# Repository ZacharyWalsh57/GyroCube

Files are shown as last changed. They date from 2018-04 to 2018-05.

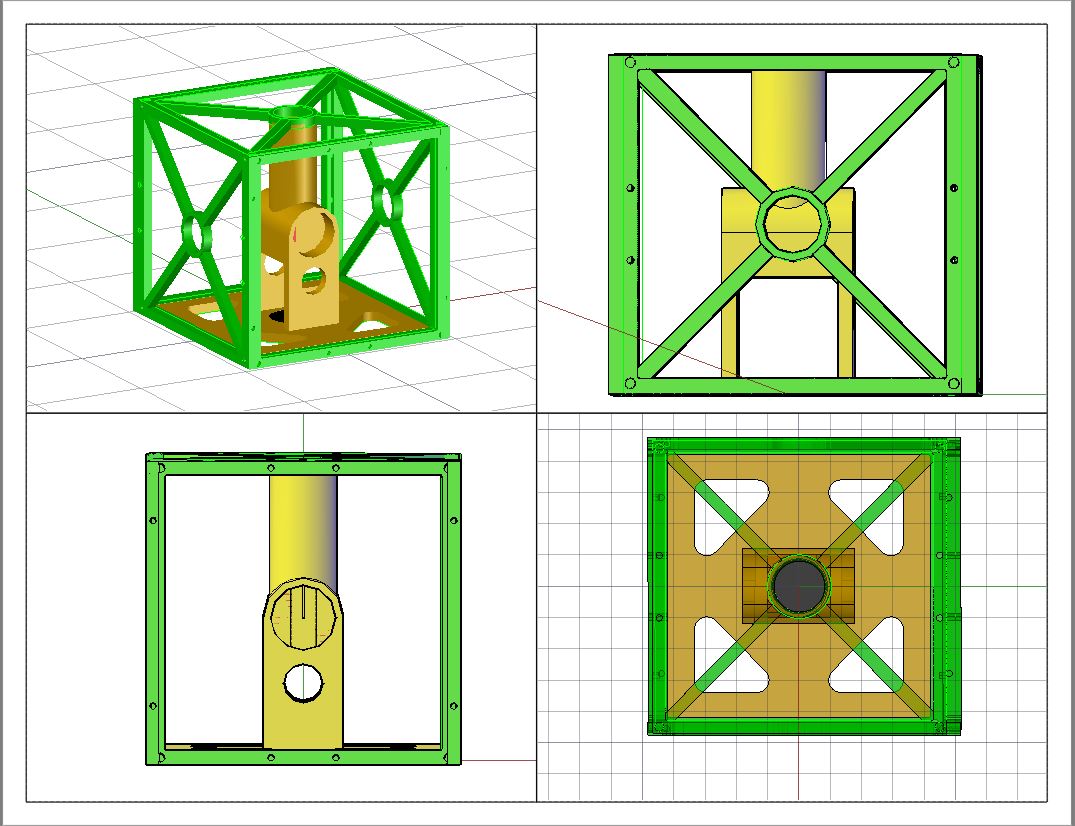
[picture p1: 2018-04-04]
3D Printing and CAD/Layout Model Views/Cube Frame V2 - Built Solid.JPG

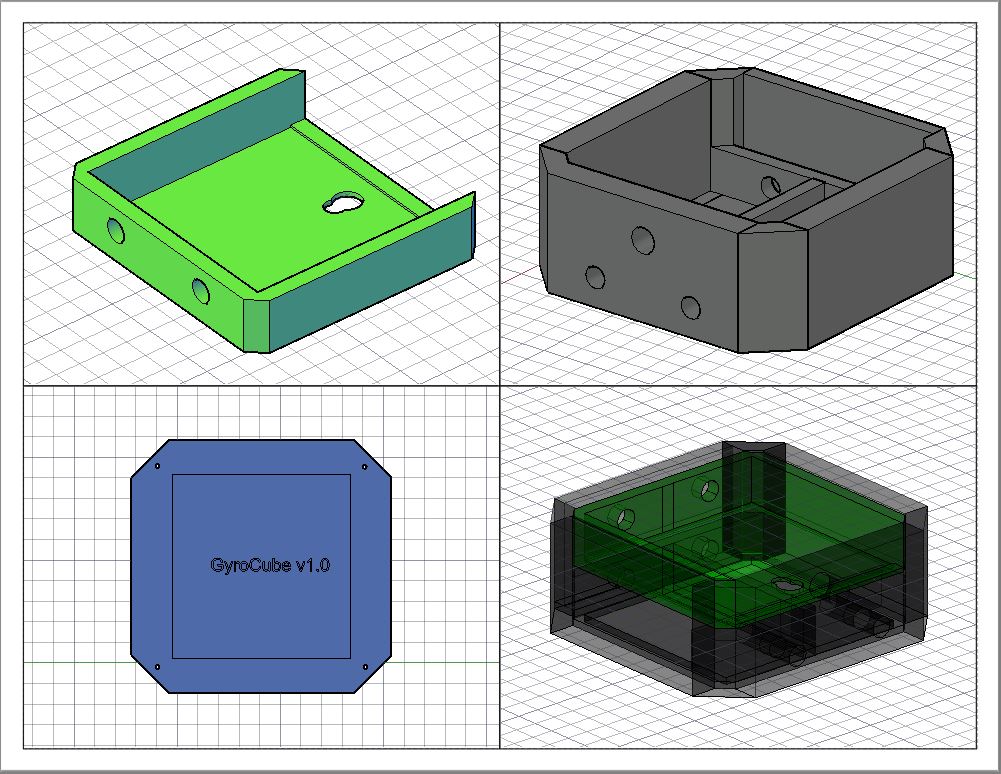
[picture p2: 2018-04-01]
3D Printing and CAD/Layout Model Views/Control Box Split View.JPG

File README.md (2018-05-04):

# GyroCube

The PID (Or maybe even PD) based, arduino powered, self balancing cube!

----------------------------------------------------------------------------------------------------------------------------------------
5/3/18:
After finally getting a new IMU and some other parts, development is back on track.  First round of progress updates is on 5/8/18.
Hopefully by then we'll have:
- A working setup loop which proves all the parts work.
- A 99% functional PID loop
- No more memory issues (Please. Running with 79% SRAM usage is painful)
- And finally, a prety good part of our presentation done. If all goes well, this might somehow work

Whats new?
- New IMU: Waveshare 10DOF IMU with an MPU9255 sensor on it (so more new libraries)
- Fully functional LCD
- Soon to be rewritten code to store more things in EEPROM and use writeMillis instead of analog write for motor speeds.

----------------------------------------------------------------------------------------------------------------------------------------

4/7/18:
It somehow didn't take that long to do a full rebuild.  The second version is up and running with stronger parts and better wiring.

Some things added now:
- PLA Soldered the parts together.  Looks bad but works wonders.
- Fixed motor vibrations
- Added in new sketch that lets us find the zero point of the MPU since we cant seem to fix the calibrations any other way.
- Also threw up diagrams for the control box and the three voltage dividers we will use for battery life monitoring.  

------------------------------------------------------------------------------------------------------------------------------------------

4/6/18:
- Well unfortunately thing took a turn for the worst.  We're left with no choice but to rebuild the whole cube from the ground up.  The repo will remain the same but will probably branch into version 1.5 leaving the main one behind. Code will be the same for basic component setup, but maybe some pins will change.  

What went wrong you might ask? Basically anything we could have imagined.
- Motor flywheels were unbalanced and caused incredible amounts of vibration.
- Hardware used to hold the cube together ripped the sides apart and caused instability.
- The MPU6050 wiring wasn't done 100% perfectly and the leads ripped out of the breakout board.
- When doing a 90% throttle test with the flywheels on, one of the flywheels heated up and expanded off of the motor completly ripping apart the entire cube.  That's the biggest problem we had.  

In the next version, as mentioned before code will remain the same for the most part, but we will likley either move to the Processing IDE or hook the system up to MATLAB (ugh) for GUI based data and tuning.

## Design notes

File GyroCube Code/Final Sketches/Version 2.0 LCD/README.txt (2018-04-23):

V2 Setup for the Cube. Going to be doing some stuff differently since
I just found out that were out of local variable space.  Anything that 
changes, thats going into the normal flash.  Anything else is staying
away. 

Wire - LEDs and I2C Mapping
Servo - Used for the ESCs.  
I2CDev - Used for addressing the MPU
MPU6050... - Used to setup the MPU.
LiquidCrystal - LCD wiring
LiquidMenu - LCD Menus (Gonna take a lot of space....)
Button - Simple button library.  Keeps code neat.
EEPROM - Storing something eventually...

------------------------------------------------------------------------
Variables:
Define all the NEVER CHANGING PINS:
LEDs pins dont move
MOTORS dont move
MOTOR pulse rates are constant.
MPU Pins dont move (Don't need to worry)
LCD Pins dont move
Button Pins do not move
MPU Variables

Then use all the menu text and write it in one shot. 
Might consider moving it into progspace if things get tight.
Really would rather not. EDIT: I did lol

Create LCD Screens and menus and the System
Create the button pins and the button objects
Create the Servos
Create the MPU
Create the LED pins
------------------------------------------------------------------------
SETUP:
Start LCD
Start Servos and attach pins
pinMode LEDs
At least init the MPU maybe?
Open Serial monitor
-print out raw debug level things
Setup Telem output (later on)
Set the LCD focus points for each display.
------------------------------------------------------------------------

HELPER FUNCTIONS:

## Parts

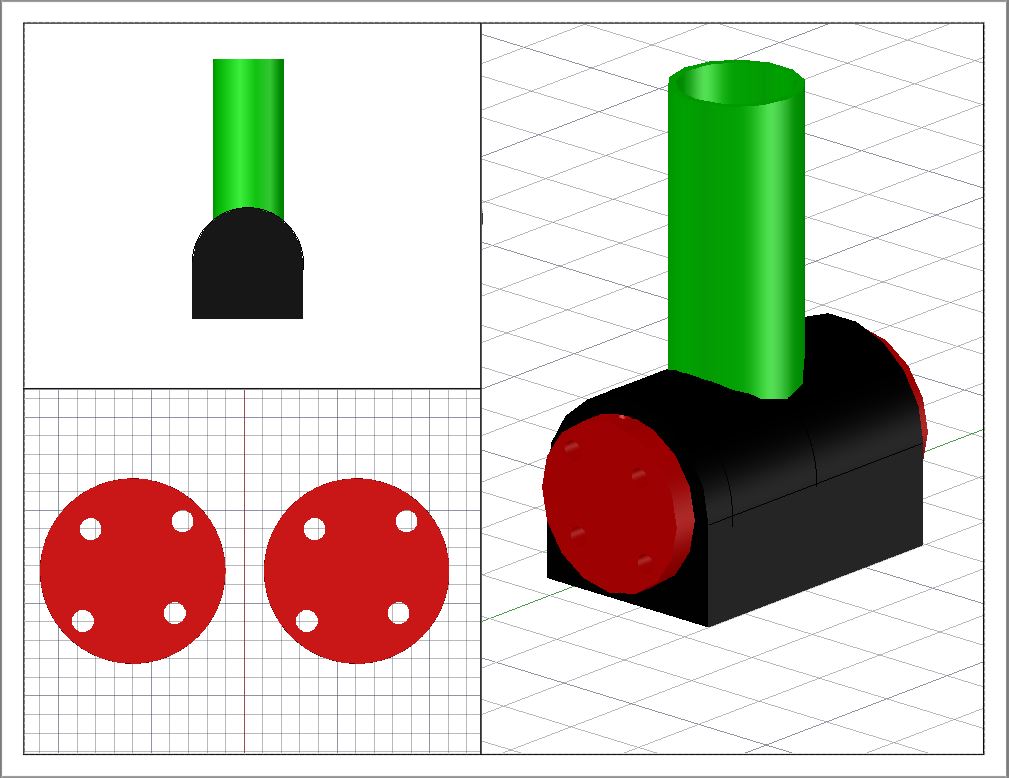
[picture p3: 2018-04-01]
3D Printing and CAD/Layout Model Views/Motor Mounting Parts.JPG

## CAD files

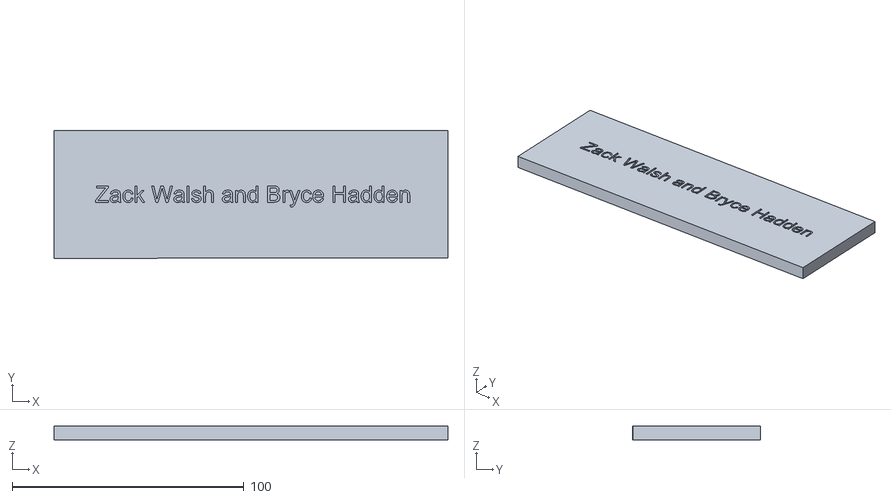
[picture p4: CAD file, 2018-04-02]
3D Printing and CAD/Battery Box Schematics/STLs/Battery Box - Top Cover - V1.stl
170.0 x 55.0 x 6.00

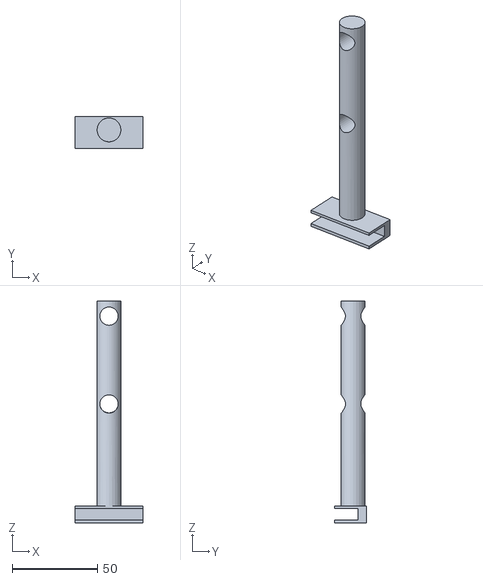
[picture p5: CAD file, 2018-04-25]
3D Printing and CAD/Control Box Schematics/STLs/Wire Clip - V3.0.stl
40.0 x 18.5 x 130.0

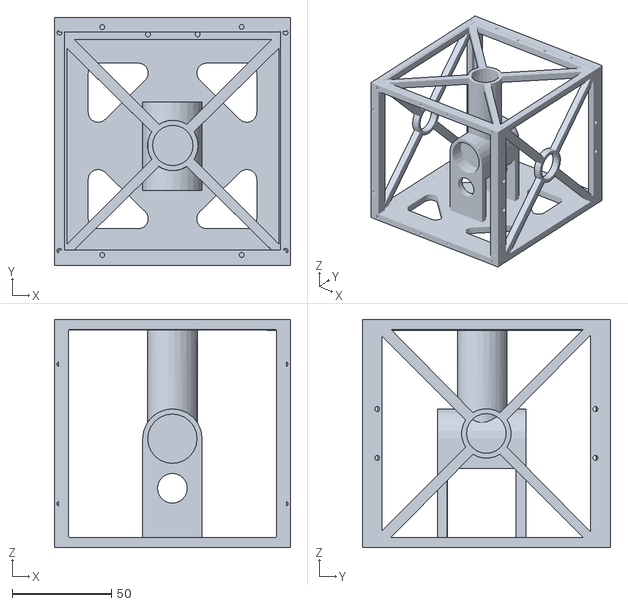
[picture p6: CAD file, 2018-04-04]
3D Printing and CAD/Cube Schematics/Version 1 - Split Parts/STLs/GyroCube Built Frame - SOLID FRAME - V2.stl
119.0 x 125.1 x 115.0

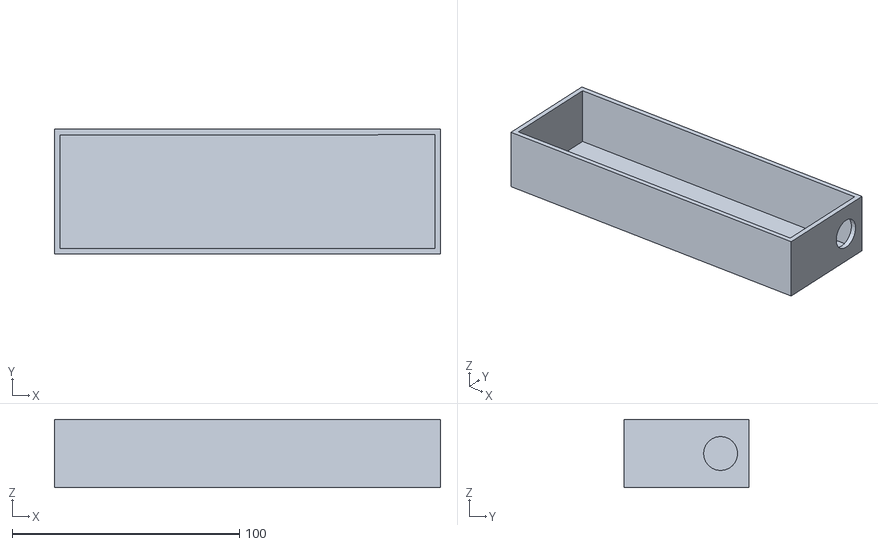
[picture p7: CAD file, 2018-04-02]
3D Printing and CAD/Battery Box Schematics/STLs/Battery Box - Bottom - V1.stl
170.0 x 55.0 x 30.0

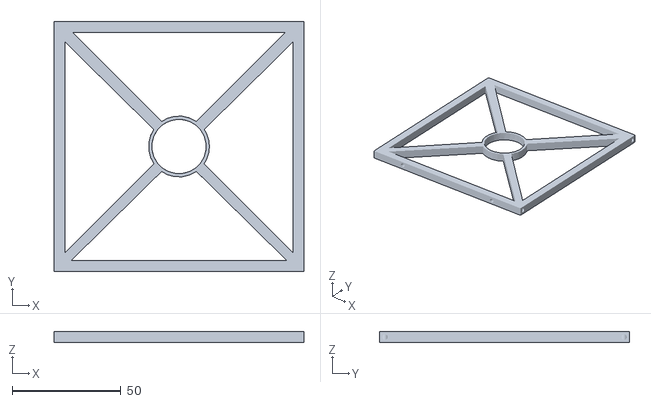
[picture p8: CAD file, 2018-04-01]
3D Printing and CAD/Cube Schematics/Version 1 - Split Parts/STLs/GyroCube TOP SIDE - STL.stl
115.0 x 115.0 x 5.14

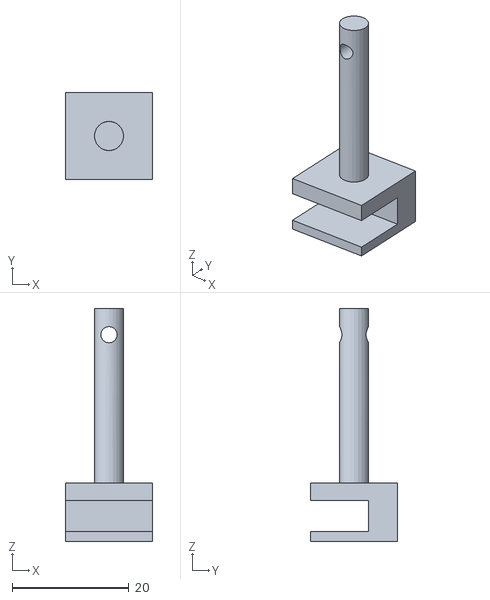
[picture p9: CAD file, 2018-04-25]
3D Printing and CAD/Control Box Schematics/STLs/Wire Clip - V1.,0.stl
15.0 x 15.0 x 40.0

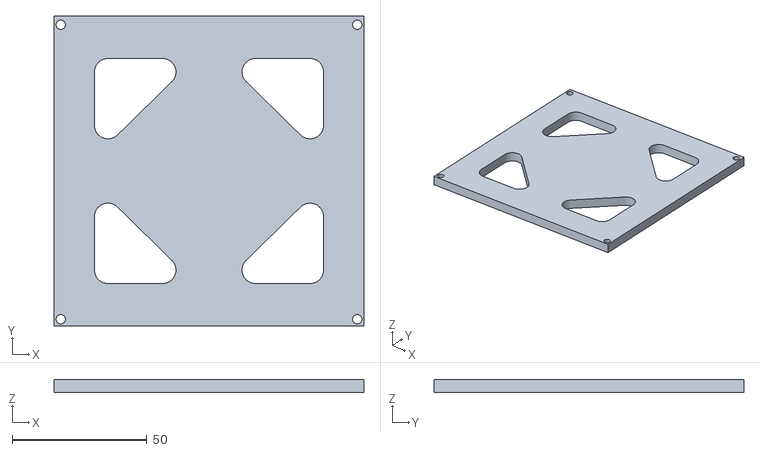
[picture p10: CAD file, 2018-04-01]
3D Printing and CAD/Cube Schematics/Version 1 - Split Parts/STLs/GyroCube Bottom Side - STL.stl
115.0 x 115.0 x 5.00

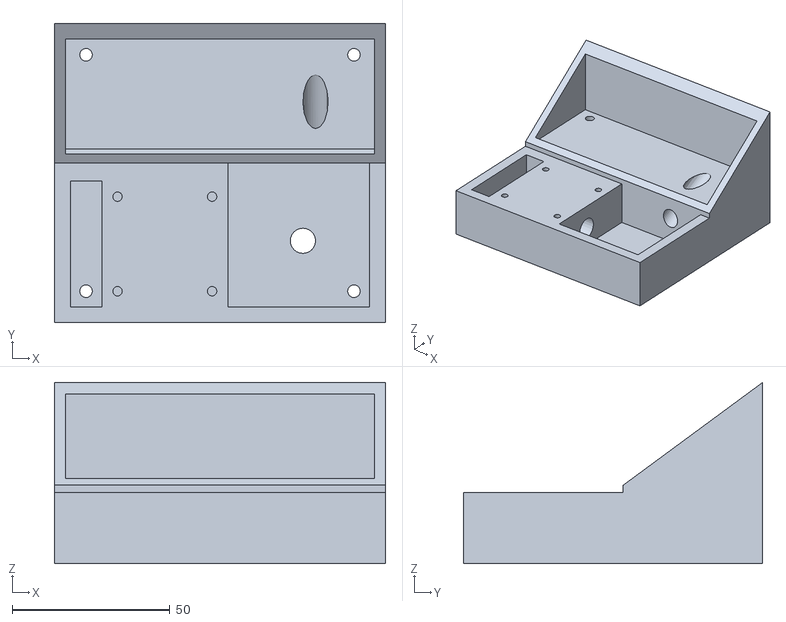
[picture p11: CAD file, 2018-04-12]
3D Printing and CAD/Control Box Schematics/STLs/LCD and KEYPAD Control Box TOP_1.stl
105.0 x 95.0 x 57.5

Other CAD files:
3D Printing and CAD/Battery Box Schematics/DWGs/Battery Box with Top.dwg
3D Printing and CAD/Control Box Schematics/CAD Drawings/Wire Clip - V1.,0.dwg
3D Printing and CAD/Cube Schematics/Version 1 - Split Parts/CAD Models/HDD Flywheel Model.dwg
3D Printing and CAD/Cube Schematics/Version 2 - Solid Prints/CAD Models/GyroCube Built Frame V2 - SOLID BOTTOM.dwg
3D Printing and CAD/Control Box Schematics/CAD Drawings/LCD and KEYPAD Control Box TOP.dwg
3D Printing and CAD/Cube Schematics/Version 1 - Split Parts/CAD Models/GyroCube Bottom Side - CAD.dwg
3D Printing and CAD/Cube Schematics/Version 2 - Solid Prints/CAD Models/GyroCube Built Frame - V2.dwg
3D Printing and CAD/Control Box Schematics/CAD Drawings/LCD and KEYPAD Control Box TOP_recover.dwg
3D Printing and CAD/Cube Schematics/Version 1 - Split Parts/CAD Models/GyroCube Open Sides EXTENDED - CAD.dwg
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

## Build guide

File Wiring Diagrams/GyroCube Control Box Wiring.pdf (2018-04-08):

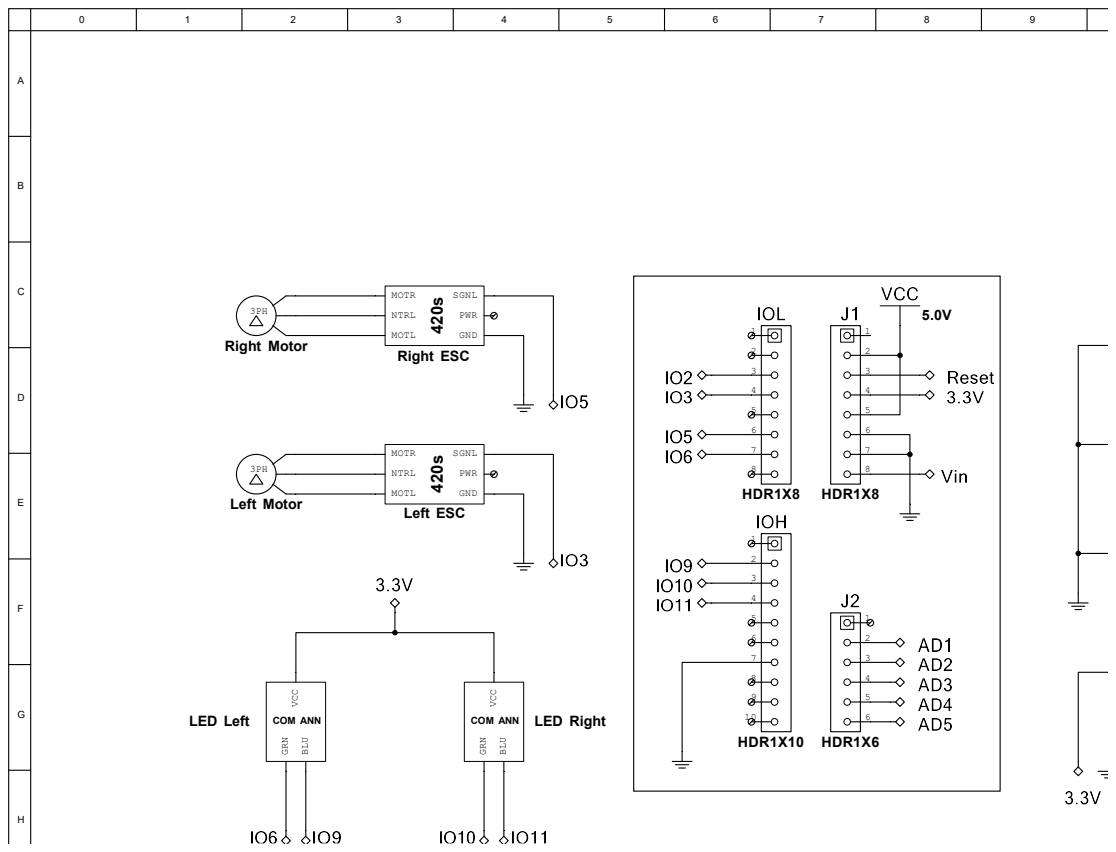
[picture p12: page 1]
HDR1X8; HDR1X10; HDR1X6; Left ESC⁴²⁰sSGNL; PWR; MOTL; GND; NTRL; MOTR; LED Left; COM ANN VCC GRN; BLU; COM ANN; LED Right VCC GRN; Right Motor; Left Motor

Right ESC ⁴²⁰sSGNL
NTRL

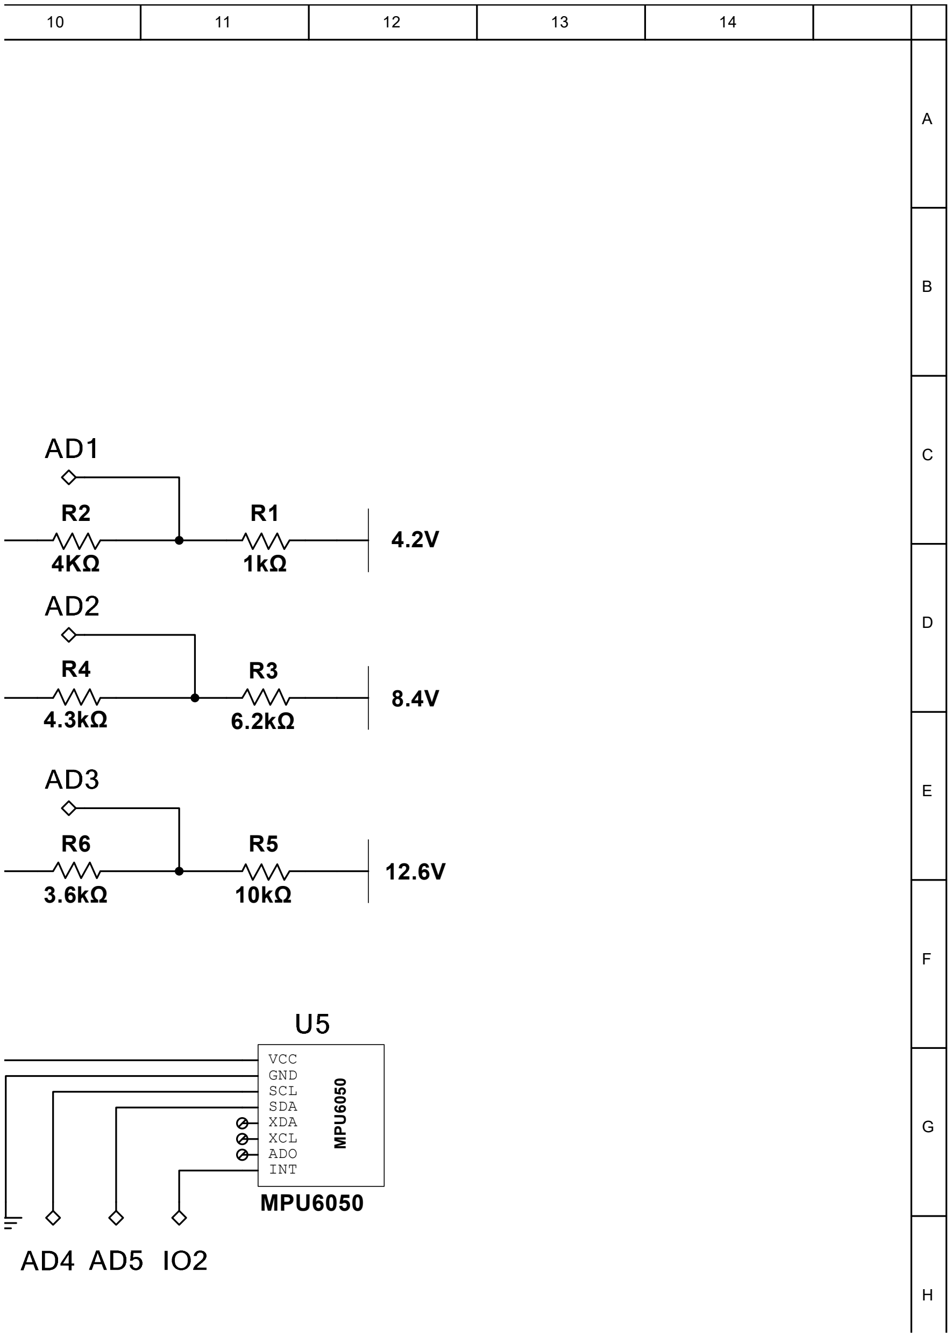
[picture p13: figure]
MPU6050MPU⁶⁰⁵⁰; VCC GND SCL SDA XDA XCL ADO INT

0 | 1 | 2 | 3 | 4 | 5 | 6 | 7 | 8 | 9

I

10 | 11 | 12 | 13 | 14 | I

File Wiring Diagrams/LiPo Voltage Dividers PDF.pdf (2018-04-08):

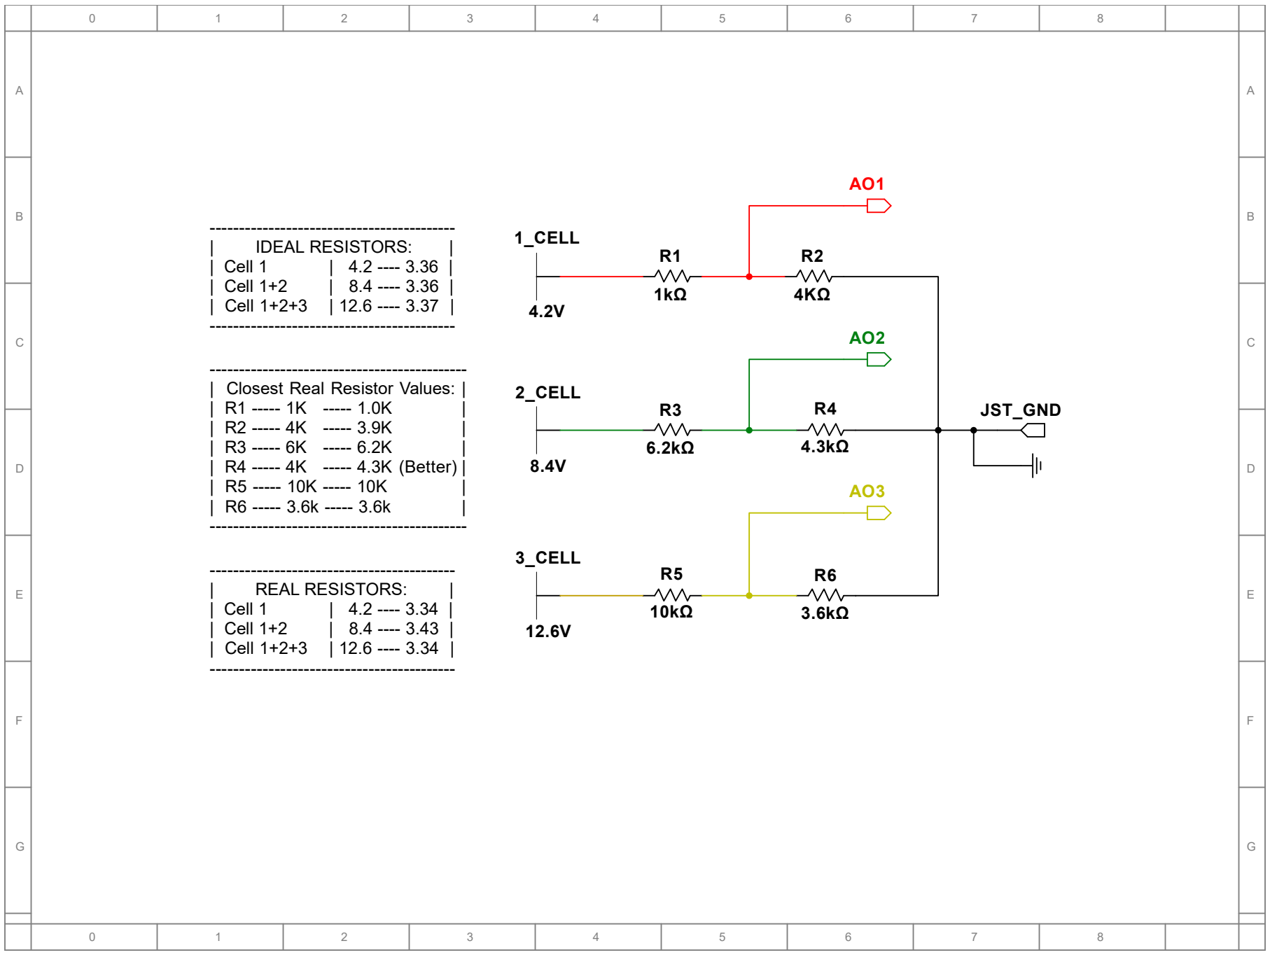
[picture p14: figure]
1_CELL; 2_CELL; 3_CELL; JST_GND; IDEAL RESISTORS:; | Cell 1; | Cell 1+2; | Cell 1+2+3 | 12.6 ---- 3.37 | ------------------------------------------; REAL RESISTORS:; | Cell 1+2+3 | 12.6 ---- 3.34 | ------------------------------------------; -------------------------------------------- | Closest Real Resistor Values: |; | R4 ----- 4K ----- 4.3K (Better) |

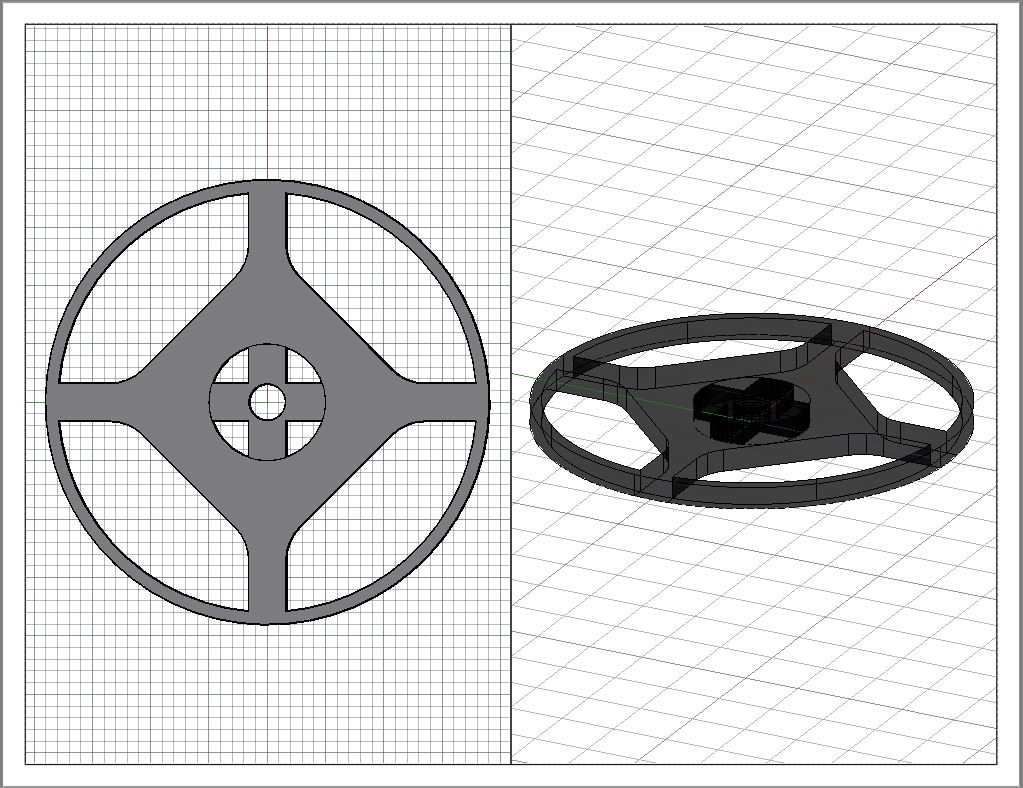
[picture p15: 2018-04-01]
3D Printing and CAD/Layout Model Views/Flywheels - Wood Prints.JPG

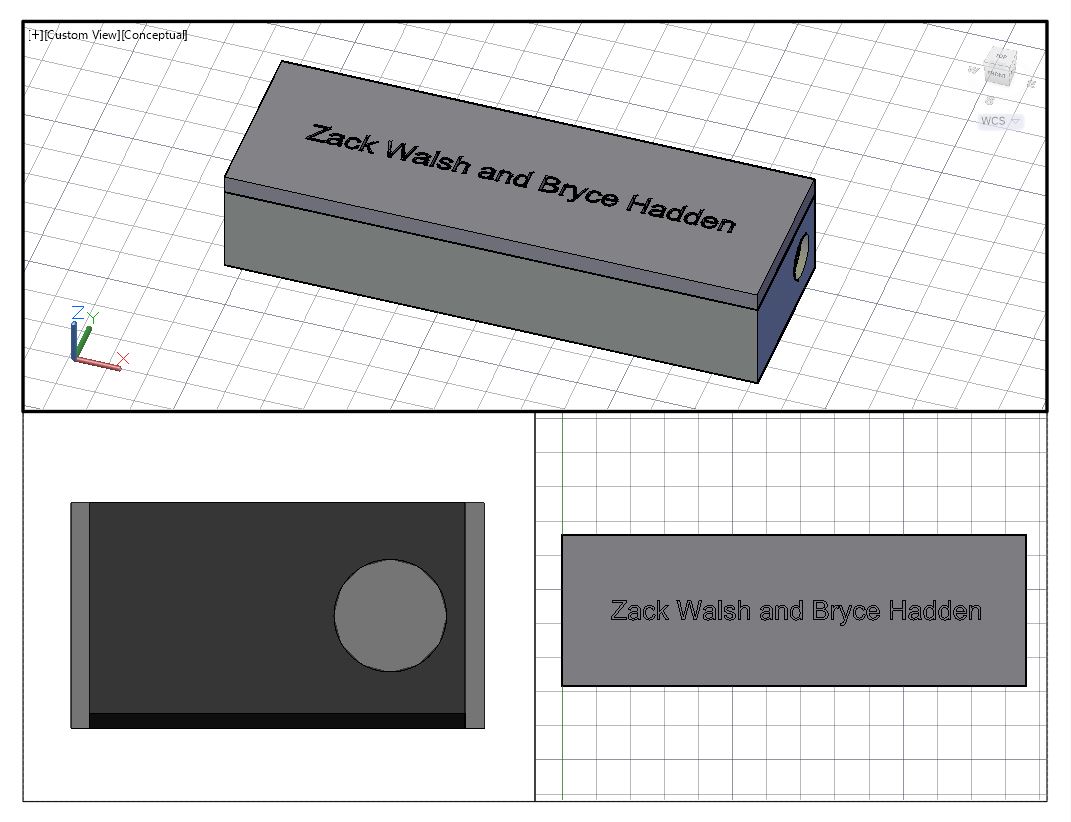
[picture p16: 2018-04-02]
3D Printing and CAD/Layout Model Views/Battery Box - Split and Built.JPG

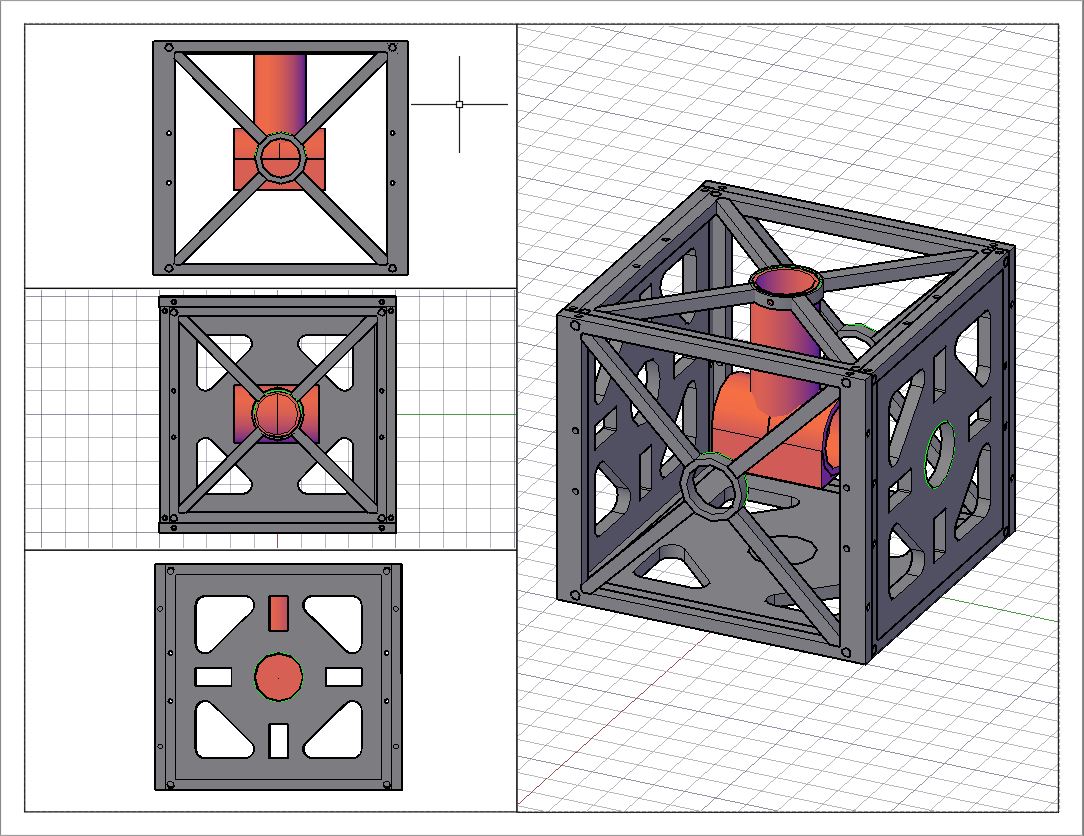
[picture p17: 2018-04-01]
3D Printing and CAD/Layout Model Views/Cube Frame - Built.JPG

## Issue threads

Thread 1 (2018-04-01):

Program the ESCs to match the firmware on the motors and write an arduino sketch to arm them.

ZackWalsh57, 2018-04-01:
Motors are linked to ESCs, will not arm still.  Given motor params invalid for some reason.  Will try to change gauge of wire from motors to ESCs and retry

ZackWalsh57, 2018-04-01:
Rewiring the ESCs with 16 AWG wire compared to the 26 I was using solved this issue. Marking closed now.

Closed 2018-04-01.

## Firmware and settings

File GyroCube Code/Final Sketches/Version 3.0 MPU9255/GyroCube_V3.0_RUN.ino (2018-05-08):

#include <Wire.h>
#include <Servo.h>
#include <Button.h>
#include <LiquidCrystal.h>
#include <LiquidMenu.h>
#include "quaternionFilters.h"
#include "MPU9250.h"

//LEDs:
#define LED_LEFT_RED 10
#define LED_LEFT_GREEN 11
#define LED_RIGHT_RED 6
#define LED_RIGHT_GREEN 9

//Motors:
Servo LEFT_MOTOR;
Servo RIGHT_MOTOR;
#define LEFT_MOTOR_PIN 3
#define RIGHT_MOTOR_PIN 5

//LCD - Screen
//RED YELLOW GREEN BLK
#define RS 0
#define EN 1
#define D4 14
#define D5 15
#define D6 16
#define D7 17

//LCD Creation:
LiquidCrystal GYROCUBE_LCD(RS,EN,D4,D5,D6,D7);

//LCD - Menu Text in PROGMEM:
const char BOOT_WELCOME_CHARS[] PROGMEM = "GyroCube 3.0";
const char BOOT_ZACK_CHARS[] PROGMEM = "Zack Walsh";
const char BOOT_BRYCE_CHARS[] PROGMEM = "Bryce Hadden";
const char MAIN_TITLE_CHARS[] PROGMEM = "GyroCube 3.0";
const char MAIN_RUN_PID_CHARS[] PROGMEM = "Press Any Button";
const char MONITOR_TITLE_CHARS[] PROGMEM = "Real-time Values";

LiquidLine BOOT_WELCOME(4,0,BOOT_WELCOME_CHARS);
LiquidLine BOOT_ZACK(5,2,BOOT_ZACK_CHARS);
LiquidLine BOOT_BRYCE(4,3,BOOT_BRYCE_CHARS);
LiquidLine MAIN_TITLE(4,0,MAIN_TITLE_CHARS);
LiquidLine MAIN_RUN_PID(2,2,MAIN_RUN_PID_CHARS);
LiquidLine MONITOR_TITLE(2,0,MONITOR_TITLE_CHARS);

//LCD - Screens:
LiquidScreen BOOT_SCREEN(BOOT_WELCOME, BOOT_ZACK, BOOT_BRYCE);
LiquidScreen MAIN_SCREEN(MAIN_TITLE, MAIN_RUN_PID);
LiquidScreen MONITOR_SCREEN(MONITOR_TITLE);

//LCD - Menus:
LiquidMenu BOOT_MENU(GYROCUBE_LCD, BOOT_SCREEN);
LiquidMenu MAIN_MENU(GYROCUBE_LCD, MAIN_SCREEN);
LiquidMenu MONITOR_MENU(GYROCUBE_LCD, MONITOR_SCREEN);

//LCD - System Menu:
LiquidSystem GYROCUBE_SYSTEM(BOOT_MENU, MAIN_MENU, MONITOR_MENU, 1);

//LCD - Button Pins
#define PULLUP true
#define INVERT true
#define DEBOUNCE 20
#define UP_PIN 4
#define DOWN_PIN 7
#define LEFT_PIN 8
#define RIGHT_PIN 12
#define MIDDLE_PIN 13

//LCD - Button Construction
Button UP(UP_PIN,PULLUP,INVERT,DEBOUNCE);
Button DOWN(DOWN_PIN,PULLUP,INVERT,DEBOUNCE);
Button LEFT(LEFT_PIN,PULLUP,INVERT,DEBOUNCE);
Button RIGHT(RIGHT_PIN,PULLUP,INVERT,DEBOUNCE);
Button MIDDLE(MIDDLE_PIN,PULLUP,INVERT,DEBOUNCE);

//MPU9255
#define INT_PIN 2
MPU9250 MPU_GYRO;
double ROLL_ANGLE;

//PID Constants:
unsigned long TIME_LAST;
double INPUT_VALUE, OUTPUT_VALUE, ERROR;
double SETPOINT = 45.0;
double I_TERM, LAST_INPUT;
double KP, KI, KD;
double OUT_MIN, OUT_MAX;
bool RUN_ALGO = true;

//---------------------------------------------------------------------------------------
//HELPER FUNCTIONS: BUTTONS, LCD, MPU, LEDS, PID, MENU ETC

//Button Sweeper for the void loop.  One run, the rest is automatic
void CHECK_BUTTONS() {
    UP.read(); 
    DOWN.read();
    LEFT.read();
    RIGHT.read();
    MIDDLE.read();
    if (UP.wasReleased())
    {
        GYROCUBE_LCD.clear();
        GYROCUBE_LCD.setCursor(5,0);
        GYROCUBE_LCD.print("SETTING UP");
        delay(500);
        INIT_PARTS();
    }
    if (DOWN.wasReleased())
    {
        GYROCUBE_LCD.clear();
        GYROCUBE_LCD.setCursor(5,0);
        GYROCUBE_LCD.print("SETTING UP");
        delay(500);
        INIT_PARTS();
    }
    if (LEFT.wasReleased())
    {
        GYROCUBE_LCD.clear();
        GYROCUBE_LCD.setCursor(5,0);
        GYROCUBE_LCD.print("SETTING UP");
        delay(500);
        INIT_PARTS();
    }
    if (RIGHT.wasReleased())
    {
        GYROCUBE_LCD.clear();
        GYROCUBE_LCD.setCursor(5,0);
        GYROCUBE_LCD.print("SETTING UP");
        delay(500);
        INIT_PARTS();
    }
    if (MIDDLE.wasReleased())
    {
        GYROCUBE_LCD.clear();
        GYROCUBE_LCD.setCursor(5,0);
        GYROCUBE_LCD.print("SETTING UP");
        delay(500);
        INIT_PARTS();
    }
}

//LED Functions to reduce code size.  RED, YELLOW, GREEN are defined
//as LEDS_*color*.  Cycle LEDS is for flashing through RGY. LEDS_OFF 
//just turns them off.  Used to make a flashing LED.
void LEDS_RED() {
    analogWrite(LED_LEFT_RED, 0);
    analogWrite(LED_LEFT_GREEN, 255);
    analogWrite(LED_RIGHT_RED, 0);
    analogWrite(LED_RIGHT_GREEN, 255);
}
void LEDS_GREEN() {
    analogWrite(LED_LEFT_RED, 255);
    analogWrite(LED_LEFT_GREEN, 0);
    analogWrite(LED_RIGHT_RED, 255);
    analogWrite(LED_RIGHT_GREEN, 0);
}
void LEDS_YELLOW() {
    analogWrite(LED_LEFT_RED, 0);
    analogWrite(LED_LEFT_GREEN, 0);
    analogWrite(LED_RIGHT_RED, 0);
    analogWrite(LED_RIGHT_GREEN, 0);
}
void CYCLE_LEDS(int DELAY) {
    LEDS_RED();
    delay(DELAY);
    LEDS_GREEN();
    delay(DELAY);
    LEDS_YELLOW();
}
void LEDS_OFF() {
    analogWrite(LED_LEFT_RED, 255);
    analogWrite(LED_LEFT_GREEN, 255);
    analogWrite(LED_RIGHT_RED, 255);
    analogWrite(LED_RIGHT_GREEN, 255);
}

//Motor throttle changes and ESC Arming. 
//NOTE: THIS SPEED SET IS ONLY FOR THE SETUP:
//Arming ESC functions
void ESC_ARMING() {
    //Arm with old stuff.  PID with the new.
    SET_SPEED(1000);
    delay(1000);
    LEDS_GREEN();
    delay(250);
    CYCLE_LEDS(375);
    LEDS_YELLOW();
    SET_SPEED(1450);
    delay(2000);
    SET_SPEED(1000);
    delay(1500);
    CYCLE_LEDS(275);
    LEDS_GREEN();   
}
void SET_SPEED(int MICROS) {
    LEFT_MOTOR.writeMicroseconds(MICROS);
    RIGHT_MOTOR.writeMicroseconds(MICROS);
}

//MPU92655 Init functions and updating RTVs when running.
void MPU9255_INIT() {
    //Setup code here I guess
    MPU_GYRO.calibrateMPU9250(MPU_GYRO.gyroBias, MPU_GYRO.accelBias);
    MPU_GYRO.initMPU9250();
    MPU_GYRO.initAK8963(MPU_GYRO.factoryMagCalibration);

    MPU_GYRO.getAres();
    MPU_GYRO.getGres();
    MPU_GYRO.getMres();

    if (MPU_GYRO.readByte(MPU9250_ADDRESS, INT_STATUS) & 0x01) {
        CYCLE_LEDS(750);
        digitalWrite(INT_PIN, LOW);
    }
    else {
        GYROCUBE_LCD.clear();
        GYROCUBE_LCD.setCursor(0,0);
        GYROCUBE_LCD.print("MPU INIT FAILED! KILLING");
        LEDS_RED();
        abort();
    }
}
void MPU9255_UPDATE() {
    if (MPU_GYRO.readByte(MPU9250_ADDRESS, INT_STATUS) & 0x01) {
        
        MPU_GYRO.readAccelData(MPU_GYRO.accelCount);  // Read the x/y/z adc values
        MPU_GYRO.ax = (float)MPU_GYRO.accelCount[0] * MPU_GYRO.aRes;
        MPU_GYRO.ay = (float)MPU_GYRO.accelCount[1] * MPU_GYRO.aRes;
        MPU_GYRO.az = (float)MPU_GYRO.accelCount[2] * MPU_GYRO.aRes;
        
        MPU_GYRO.readGyroData(MPU_GYRO.gyroCount);  // Read the x/y/z adc values
        MPU_GYRO.gx = (float)MPU_GYRO.gyroCount[0] * MPU_GYRO.gRes;
        MPU_GYRO.gy = (float)MPU_GYRO.gyroCount[1] * MPU_GYRO.gRes;
        MPU_GYRO.gz = (float)MPU_GYRO.gyroCount[2] * MPU_GYRO.gRes;
        
        MPU_GYRO.readMagData(MPU_GYRO.magCount);  // Read the x/y/z adc values
        MPU_GYRO.mx = (float)MPU_GYRO.magCount[0] * MPU_GYRO.mRes
               * MPU_GYRO.factoryMagCalibration[0] - MPU_GYRO.magBias[0];
        MPU_GYRO.my = (float)MPU_GYRO.magCount[1] * MPU_GYRO.mRes
               * MPU_GYRO.factoryMagCalibration[1] - MPU_GYRO.magBias[1];
        MPU_GYRO.mz = (float)MPU_GYRO.magCount[2] * MPU_GYRO.mRes
               * MPU_GYRO.factoryMagCalibration[2] - MPU_GYRO.magBias[2];
               
        MPU_GYRO.updateTime();
        
        MahonyQuaternionUpdate(MPU_GYRO.ax, MPU_GYRO.ay, MPU_GYRO.az, MPU_GYRO.gx * DEG_TO_RAD,
                         MPU_GYRO.gy * DEG_TO_RAD, MPU_GYRO.gz * DEG_TO_RAD, MPU_GYRO.my,
                         MPU_GYRO.mx, MPU_GYRO.mz, MPU_GYRO.deltat);
        
        MPU_GYRO.delt_t = millis() - MPU_GYRO.count;

        MPU_GYRO.roll  = atan2(2.0f * (*getQ() * *(getQ()+1) + *(getQ()+2)
                    * *(getQ()+3)), *getQ() * *getQ() - *(getQ()+1)
                    * *(getQ()+1) - *(getQ()+2) * *(getQ()+2) + *(getQ()+3)
                    * *(getQ()+3));
        MPU_GYRO.roll *= RAD_TO_DEG;
        ROLL_ANGLE = abs(MPU_GYRO.roll);
        //Serial.println(ROLL_ANGLE);
    }
}

//Finally make sure all the parts are working right in one big init function.
void INIT_PARTS() {
    CYCLE_LEDS(750);
    STRING_ON_LCD(0,1,"LEDS SETUP",false);
    //GYROCUBE_LCD.setCursor(0, 1);
    //GYROCUBE_LCD.print("LEDS SETUP");
    
    MPU9255_INIT();
    MPU9255_UPDATE();
    //GYROCUBE_LCD.setCursor(0, 2);
    //GYROCUBE_LCD.print("MPU9255 DMP OK");
    STRING_ON_LCD(0,2,"MPU9255 DMP OK",false);

    ESC_ARMING();
    //GYROCUBE_LCD.setCursor(0, 3);
    //GYROCUBE_LCD.print("ESCs ARMED");
    STRING_ON_LCD(0,3,"ESCs ARMED",false);
    delay(750);
    
    GYROCUBE_LCD.clear();
    CYCLE_LEDS(250);
    PID_ALGO();
    //Then finally, throw this bitch on autopilot lol
}

//PID FUNCTIONS: These functions are pretty fuckin dope if you ask me. Credit to Brett Beauregard for some basic help/explaining. (Spelling lol)
void PID_ALGO() {
    CYCLE_LEDS(750);
    SET_OUTPUT_LIMITS(2000, 1250);
    SET_TUNINGS(5.43, 0.42, 4.43);
    CYCLE_LEDS(1000);
    delay(500);
    SET_SPEED(1100);
    
    GYROCUBE_SYSTEM.change_menu(MONITOR_MENU);
    STRING_ON_LCD(0,1,"Kp",false);
    STRING_ON_LCD(9,1,"SP",false);

    STRING_ON_LCD(0,2,"Ki",false);
    STRING_ON_LCD(9,2,"RT",false);

    STRING_ON_LCD(0,3,"Kd",false);
    STRING_ON_LCD(9,3,"EV",false);
    
    delay(2000);
    MPU9255_UPDATE();
    while(RUN_ALGO) {
        PID_COMPUTE();
    }
}
void SET_OUTPUT_LIMITS(double MAX, double MIN) {
    if(MIN > MAX)
        return;
    OUT_MAX = MAX;
    OUT_MIN = MIN;

    if(OUTPUT_VALUE > OUT_MAX)
        OUTPUT_VALUE = OUT_MAX;
    else if(OUTPUT_VALUE < OUT_MIN)
        OUTPUT_VALUE = OUT_MIN;

    if(I_TERM > OUT_MAX) 
        I_TERM = OUT_MAX;
    else if(I_TERM < OUT_MIN)
        I_TERM = OUT_MIN;
}
void SET_TUNINGS(double SKP, double SKI, double SKD) {
    if (SKP < 0 || SKI < 0 || SKD < 0) {
        return;
    }
    KP = SKP;
    KI = SKI;
    KD = SKD;
}
void FETCH_NEW_DATA() {
    //Fetch the latest angle values
    MPU9255_UPDATE();
    INPUT_VALUE = ROLL_ANGLE;
}
void PID_COMPUTE() {
    CHECK_HALT();
    FETCH_NEW_DATA();
    //PID computation in here:
    unsigned long NOW = millis();
    int ELAPSED = (NOW - TIME_LAST);

    //Make sure its time for new samples.
    //Compute Working Variables now:
    ERROR = SETPOINT - INPUT_VALUE;
    I_TERM += (KI * ERROR);
    if(I_TERM > OUT_MAX)
        I_TERM = OUT_MAX;
    else if(I_TERM < OUT_MIN)
        I_TERM = OUT_MIN;
    double D_INPUT = (INPUT_VALUE - LAST_INPUT);

    //Convert this over to PID Components here:
    OUTPUT_VALUE = KP * ERROR + I_TERM - KD * D_INPUT;
    if (OUTPUT_VALUE > OUT_MAX)
        OUTPUT_VALUE = OUT_MAX;
    else if (OUTPUT_VALUE < OUT_MIN)
        OUTPUT_VALUE = OUT_MIN;

    //Take note of some important values:
    LAST_INPUT = INPUT_VALUE;
    TIME_LAST = NOW;

    //Write the new value to the motors:
    PID_MOTORS();

    DOUBLE_ON_LCD(12,1,SETPOINT,false);
    DOUBLE_ON_LCD(12,2,INPUT_VALUE,false);
    DOUBLE_ON_LCD(12,3,ERROR,false);
    DOUBLE_ON_LCD(3,1,KP,false);
    DOUBLE_ON_LCD(3,2,KI,false);
    DOUBLE_ON_LCD(3,3,KD,false);
}
unsigned int SPEED_CONVERSION(float DEGREE) {
    return 1000 + (DEGREE * 150 + 13) / 27;
}
void PID_MOTORS() {
    //Motor write values. Take care of this later on. 
    //Double check all the new code/make sure it compiles.
    //Code compiles.  This function is gonna be tough since they spin
    //against each other. So we have to make it so that if we add to one 
    //and remove from another.  Not hard.  Just annoying.
    if(ERROR > 0) {
        double RIGHT_SPEED = SPEED_CONVERSION(RIGHT_MOTOR.read());
        double DIFFERENCE_RIGHT = (OUTPUT_VALUE - RIGHT_SPEED);
        RIGHT_MOTOR.writeMicroseconds(OUTPUT_VALUE - DIFFERENCE_RIGHT);
        LEFT_MOTOR.writeMicroseconds(OUTPUT_VALUE);
    }
    if(ERROR < 0) {
        double LEFT_SPEED = SPEED_CONVERSION(LEFT_MOTOR.read());
        double DIFFERENCE_LEFT = (OUTPUT_VALUE - LEFT_SPEED);
        RIGHT_MOTOR.writeMicroseconds(OUTPUT_VALUE);
        LEFT_MOTOR.writeMicroseconds(OUTPUT_VALUE - DIFFERENCE_LEFT);
    }
}
void CHECK_HALT() {
    UP.read(); 
    DOWN.read();
    LEFT.read();
    RIGHT.read();
    MIDDLE.read();
    if (UP.wasReleased())
    {
        PID_HALTED();
    }
    if (DOWN.wasReleased())
    {
        PID_HALTED();
    }
    if (LEFT.wasReleased())
    {
        PID_HALTED();
    }
    if (RIGHT.wasReleased())
    {
        PID_HALTED();
    }
    if (MIDDLE.wasReleased())
    {
        PID_HALTED();
    }

}
void PID_HALTED() {
    RUN_ALGO = !RUN_ALGO;
    LEDS_OFF();
    SET_SPEED(1300);
    delay(1000);
    SET_SPEED(1000);
    STRING_ON_LCD(0,0, "PID LOOP HALTED", true);
    while(!RUN_ALGO) {
        LEDS_RED();
        delay(750);
        LEDS_OFF();
        delay(750);
    }
}

//LCD UPDATE Function.  Give two ints, a string or double and a boolean for clear or not.
//Might help cut down on code size. 
void STRING_ON_LCD(int COLL, int ROW, String TEXT, bool CLEAR) {
    if(CLEAR) {
        GYROCUBE_LCD.clear();
    }
    GYROCUBE_LCD.setCursor(COLL, ROW);
    GYROCUBE_LCD.print(TEXT);
}
void DOUBLE_ON_LCD(int COLL, int ROW, double VALUE, bool CLEAR) {
    if(CLEAR) {
        GYROCUBE_LCD.clear();
    }
    GYROCUBE_LCD.setCursor(COLL, ROW);
    GYROCUBE_LCD.print(VALUE);
}


//--------------------------------------------------------------------------------------------------------------------------------------------------------------
//RUNTIME CODE:

void setup() {
    //SERIAL MONITOR AND LCD DONT WORK AT THE SAME TIME.  DAMN IT.
    //Debugging purposes.
    //Serial.begin(38400);

    Wire.begin(); //For the MPU9255

    //Fire up LEDs:
    pinMode(LED_LEFT_RED, OUTPUT);  //LEFT RED PIN OUT
    pinMode(LED_LEFT_GREEN, OUTPUT);  //LEFT GREEN PIN OUT
    pinMode(LED_RIGHT_RED, OUTPUT); //RIGHT RED PIN OUT
    pinMode(LED_RIGHT_GREEN, OUTPUT); //RIGHT GREEN PIN OUT
    delay(350);

    //Motor Connections and arming
    LEFT_MOTOR.attach(LEFT_MOTOR_PIN);
    RIGHT_MOTOR.attach(RIGHT_MOTOR_PIN);
    SET_SPEED(1000);
    delay(250);

    //Setup the MPU9255:
    pinMode(INT_PIN, INPUT);
    digitalWrite(INT_PIN, LOW);
    delay(350);

    //LCD Start:
    delay(1500);
    GYROCUBE_LCD.begin(20,4);

    //Setup PROGMEM Char sets to Strings:
    BOOT_WELCOME.set_asProgmem(1);
    BOOT_ZACK.set_asProgmem(1);
    BOOT_BRYCE.set_asProgmem(1);
    MAIN_TITLE.set_asProgmem(1);
    MAIN_RUN_PID.set_asProgmem(1);
    MONITOR_TITLE.set_asProgmem(1);

    //LCD Show Splash and Pause, then update:
    GYROCUBE_SYSTEM.change_menu(BOOT_MENU);
    delay(5000);
    GYROCUBE_SYSTEM.change_menu(MAIN_MENU);

    //System update:
    GYROCUBE_SYSTEM.update();
    CYCLE_LEDS(750);

}
//Simple ass void loop lol
void loop() {
    //Check ya buttons
    CHECK_BUTTONS();
}

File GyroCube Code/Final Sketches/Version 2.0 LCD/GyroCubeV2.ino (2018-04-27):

/*GYROCUBE V2.0 Setup
Not a whole lot to explain here but it can't hurt to just throw the basics down here:
The best way to go about it is just explaining by blocks of code/lines.  So here it goes

--------------------------------------------------------------------------------------------------

Begins at #include <... and ends at menu.h>:
These are the included Library files for the program to run correctly.  Each one IS critical.
---- Wire:          Used for the LEDs, the MPU Serial comms, and the LCD Pinnout.  Probably the
                    most important but most simple Library we used here.
---- Servo:         Used for the motor ESCs.  They use PPM so Servo is used instead of
                    a traditional setup of using digital write to send PWM (More on the Wiki)
---- I2CDev:        Used for the MPU connections and the LCD (Somehow. No idea how lol)
                    MPU runs serial data on SDA and SCL with pin D2 (P3) as an interupt.
                    FIFO buffer is in place to keep things orderly and read the serial data
                        Since the angle readings are sent via I2C, they come in 2 packets of 8
                        bits. This means we have to parse them somehow. Thats where FIFO comes into
                        the equiation.
---- MPU6050:       Not gonna lie, this is complex as fuck so stay with me here. This Library does
                    all the heavy lifting behind the scenes. Converting packets to floats,
                    initializing the DMP (Digital Motion Processor), watching for FIFO overflow
                    and more. As always credit is given where it's due, Thanks to jrowberg on GitHub
                    for his work on this Library which makes this project possible honestly.
---- Button:        Library I wrote in my spare time (which I have wayyy too much of) that allows/
                    easy creation of a hardware button on the Arduino.  Library uses a class of Button
                    and on construction and object type of button is given a pin, a boolean for if 
                    we are using pullup resistors and an int for a debounce time in MS to stop us
                    from picking up noise on the signal.
---- LqdCryst/Menu: Both of these fall under the same category so I'll explain them both 
                    here.  LiquidCrystal is responsible for making an object of LCD which is assigned
                    various pins for TX,RX, Data lines, and so on.
                    The LCD works something like this:
                        We used an old LCD/SD/Button combo off of a 3D printer that I bricked (whoops lol) so 
                        contrast and backlight were taken care of by the board that the LCD was on.
                        Interestingly, there's both a 7409 SR which would have potentially given us I2C 
                        connections and only used 2 pins, but it seems like it's big time burned out. The 
                        LiquidCrystal Library reads the pins we give the object of LCD and then is able to convert 
                        our ASCII characters (fancy for text) into digital bytes/encoded chars for the LCD to 
                        display.  The RS and EN lines are for realtime display so we can update the display in 
                        real time.

---------------------------------------------------------------------------------------------------------------

Begins with #define LED_LEFT... and ends at MIDDLE_PIN 13:
These lines are used for us to define some values we need throughout the program.
----  LEDS:         Pins needed for the LEDs to change color.  They are common annode meaning both colors
                    inside the LED share a common 5v+ input and use seperate grounds. So even though it says
                    that I'm giving 5V on the red pin, it's actually the green LED getting power. As some of you 
                    may or may not know already, when you feed a voltage into and LED thats in reverse bias, 
                    you actually create a resistance large enough that it seems like an open has been created 
                    and thus we end up turning off that color led.  And by using PWM signals, we can even create a small 
                    resistance that lets us dim an LED so we can make any combination of hues from Red and Green.

                        __________________________________________________________
                        |                   COMMON ANNODE LED                    |  If we set PIN_10 to 5v and PIN_11 to 0v,
                        |               PIN_10 = RED, PIN_11 = GREEN             |  then we allow 5v through PIN_11 and
                        |                                                        |  and block 5v on PIN_10 so we only have
                        |             GND       ================                 |  a complete circuit to ground on PIN_10
                        |     <| --- PIN_11 --- |-- GRN_WIRE ++|                 |  therefore only the green LED is powered
                        |                       |              | +++ 5v +++ ||   | 
                        |     <| --- PIN_10 --- |-- RED_WIRE ++|                 |  The same applies in for turning on the red
                        |             GND       |==============|                 |  LED except PIN_11 shows +5v and PIN_10 is 0v
                        |________________________________________________________|

---- MOTORS:        Code used to setup the ESCs for the 2312 motors inside the cube itself. Normally a motor is driven
                    by using either a variable current input (Pot to change how much resistance is shown to the motor)
                    or by using PWM which pulses a digital signal of 5v highs and 0v lows which the motor reads as an RPM.
                    In our case, the ESCs I am using are from an old drone that I built a while ago and didn't need to fly.
                    These are DJI 420s 30A ESCs which are made to run either a 2312 or 2212 motor depending on how they are
                    programmed.  These ESCs do way more than I would need them to do (active braking, velocity control, etc)
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

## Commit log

2018-04-01 Upload All Code and Files
    Upload all the code thus far and the DWGs/STLs/JPGs that have been made so far.
    Development is paused for now while the Wiki and Project Boards are updated and created
    [CCW-Prop Nut.stl, CW-Prop Nut.stl, Control Box - V1.0 - MORE NARROW.stl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]
2018-04-01 Cleanup Extra Files
    Removed a good amount of clutter that was originally in the repo. Should still be complete
    [Control Box - V1.0 - MORE NARROW.stl, Control Box - V1.0 - Narrow.stl, Control Box - V1.0.dwg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]
2018-04-02 Change Repo Structure (AGAIN)
    Made more changes to repo layout and worked on the Project Boards some more
    [CCW-Prop Nut.stl, CW-Prop Nut.stl, Control Box - V1.0.dwg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]
2018-04-02 More Structure Changes
    Same old same old
    [Control Box - V1.0.dwg, Control Box - V1.0.stl, Control Box - V1.5 - Less Walls.stl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]
2018-04-02 Moldify setup sketch. Should work as epxected when motors are being armed.
2018-04-02 Begin working on the battery life sketches. Added in the STLs and DWGs
    [Battery Box - Bottom - V1.stl, Battery Box - Top Cover - V1.stl, Battery Box with Top.dwg]
2018-04-03 General Setup code is complete. Needs battery cell monitoring included.
2018-04-03 Remove Arm Delay
    Removed the delay after arming which caused one of the motors to not spin
2018-04-04 Massive Structure Update: Moved a lot of files around. Cube V2
    [CCW-Prop Nut.stl, CW-Prop Nut.stl, GryoCube Cross Motor Mount - STL.stl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]
2018-04-06 Update files currently inside the repo
    Just pushing the latest versions just in case we forgot something in the last major update.
    [GyroCube Built Frame - V2 TOP.stl, GyroCube Built Frame V2 - SOLID BOTTOM.dwg]
2018-04-08 V2 is Up!
    Version two of the cube has been completed finally!
    Complete rebuild, rewired the control box, and added in a new sketch which can automatically find a "zero" point on the MPU since we have some sort of odd offset by about 1-2.15
    Also added in wiring diagrams for the control box and the three voltage regulators we are going to use to read the voltage from the three LiPo cells
    [GyroCube Built Frame V2 - TOP.dwg, GyroCube NO FILL Sides - CAD.stl]
2018-04-10 More work on the LCD
    More work on the LCD module. May appear to have a bad HCF4094B module.
    ASICC/any other characters do not decode correcty. Lies strictly in the module. Need to try direct wiring next.
2018-04-12 Setup the LCD and keypad finally.
    [Control Box - V3.0.dwg, Control Box - V3.0_recover.dwg, LCD and KEYPAD Control Box TOP Plate1.stl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]
2018-04-23 More Work
    More code changes. Version 2.0 setup compiles and runs just as expected. All that remains is the PID loop
2018-04-25 Finsih Setup V2.0!
    [Wire Clip - V1.,0.dwg, Wire Clip - V1.,0.stl, Wire Clip - V2.0.stl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]
2018-04-27 Update V2 Setup
    V2 Setup is pretty much done now. Just have to add the PID Loop and replace the MPU6050. Seems like I burnt it out or ruined one of the pin holes accidentally. See GyroCubeV2.ino for more
    [GyroCubeV2.ino]
2018-05-04 Version 3.0 is live!
    [GyroCube 10DOF IMU Mount - V2.stl, GyroCube 10DOF IMU Mount - V3.stl, GyroCube 10DOF IMU Mount - V4.stl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]
2018-05-04 Finish the V3 Sketch
    V3 Setup is DONE. All parts work as wanted, and the PID loop is in the code. Needs tuning and some motor functions added in, but overall it's done.
2018-05-08 Made final changes to code and Schematics
    Presentations begin today. I think? If they do we're kinda screwed but kinda not. PID loop works, motors spin, but we dont have any flywheels.
    [HDD Flywheel Model.dwg]
2018-05-09 Added in new Cube Factory file
    A one part cubr factory file. Hopefully going to be printed later this week.
    Progress went well. Motor mount broke but can be fixed
